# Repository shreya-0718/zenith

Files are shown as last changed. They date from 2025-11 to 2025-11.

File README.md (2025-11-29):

# zenith
### An STM32-based flight controller!
front

I made this project to explore more advanced hardware and firmware :)
Also, to get experience with the STM32 and its IDEs.

## Features:
- USB-C 
- MicroSD Card
- Servos: Two PWM Channels
- Sensors: I²C barometer (BMP580) and charger (BQ25883), SPI IMU (ICM-45686)
- Two programmable LEDs

## To Use:
- Install STM32CubeIDE here: https://www.st.com/en/development-tools/stm32cubeide.html
- Use the code in here as a starter, and build from there!
- Use the schematic below as a guide.

## Images:
full schem
stm32 schem
<br>
pcb!

<br>

front
back

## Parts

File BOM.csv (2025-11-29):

Item | Description | Link | Cost | Quantity
BMP580 | Barometric pressure sensor | https://www.lcsc.com/product-detail/C22391138.html | 1.08 | 1
Resistor | 330 | https://www.lcsc.com/product-detail/C105881.html | 0.12 | 1
LED | WS2812B-2020 SMD | https://www.lcsc.com/product-detail/C965555.html | 0.08 | 2
Capacitor | 1uF | https://jlcpcb.com/partdetail/53938-CL05A105KA5NQNC/C52923 | 0.01 | 4
Resistor | 5.1 K | https://jlcpcb.com/partdetail/26648-0402WGF5101TCE/C25905 | 0.01 | 2
Resistor | 10 | https://jlcpcb.com/partdetail/26487-0402WGF1002TCE/C25744 | 0.01 | 14
Capacitor | 100nF | https://jlcpcb.com/partdetail/1877-CL05B104KO5NNNC/C1525 | 0.01 | 11
Capacitor | 44nF | https://www.lcsc.com/product-detail/C49326689.html | 0.54 | 1
Capacitor | 10uF | https://jlcpcb.com/partdetail/2043-CL10A106MQ8NNNC/C1691 | 0.01 | 8
ICM-45686 | Motion sensor | https://www.lcsc.com/product-detail/C22459454.html | 8.55 | 1
TS-1088-AR02016 | Button | https://www.lcsc.com/product-detail/C720477.html | 0.08 | 2
Capacitor | 0.1uF | https://www.lcsc.com/product-detail/C76934.html | 0.12 | 1
Resistor | 100k | https://www.lcsc.com/product-detail/C60491.html | 0.06 | 1
Inductor | 1uH | https://www.lcsc.com/product-detail/C435392.html | 0.5 | 1
Capacitor | 22uF | https://www.lcsc.com/product-detail/C602037.html | 0.024 | 5
Screw Terminal | 01x02 | https://www.lcsc.com/product-detail/C557685 | 1.15 | 1
Connector | 01x03 | https://jlcpcb.com/partdetail/-PinSocket_1x03_P254mm_Vertical/C9900002703 | 0.01 | 2
Capacitor | 2.2uF | https://jlcpcb.com/partdetail/13164-CL05A225MQ5NSNC/C12530 | 0.0024 | 2
Resistor | 22.1k | https://jlcpcb.com/partdetail/YAGEO-RC0201FR0722K1L/C142019 | $0.00 | 1
Crystal Oscillator | 25MHz | https://jlcpcb.com/partdetail/YXC_CrystalOscillators-X322525MOB4SI/C9006 | 0.07 | 1
BQ25883RGER | Charging IC | https://jlcpcb.com/partdetail/TexasInstruments-BQ25883RGER/C544362 | 4.47 | 1
LED | Indicator | https://jlcpcb.com/partdetail/EverlightElec-16_213SDRC_S530_A3TR8/C71911 | 0.03 | 1
TF-01A | Micro SD Card | https://jlcpcb.com/partdetail/Korean_HropartsElec-TF01A/C91145 | 0.17 | 1
Resistor | 5.23k | https://jlcpcb.com/partdetail/301853-RC01W5231FT/C320948 | 0.001 | 1
Capacitor | 47uF | https://www.lcsc.com/product-detail/C49326689.html | 0.54 | 1
Capacitor | 20pF | https://jlcpcb.com/partdetail/72988-0201CG200J500NT/C71879 | 0.0007 | 4
Resistor | 10k | https://jlcpcb.com/partdetail/LIZElec-CR0201FH1002G/C100126 | 0.0005 | 1
LMR51431 | Power Management | https://jlcpcb.com/partdetail/TexasInstruments-LMR51430XDDCR/C5185863 | 0.97 | 1
Resistor | 30.1k | https://jlcpcb.com/partdetail/YAGEO-RC0201FR0730K1L/C273278 | 0.0008 | 1
Q13FC1350000401 | Crystal Oscillator | https://jlcpcb.com/partdetail/SeikoEpson-Q13FC1350000400/C49109464 | 0.25 | 1
FCM1608KF-601T04 | Ferrite Bead | https://jlcpcb.com/partdetail/TAITECH-FCM1608KF601T03/C141723 | 0.0046 | 1
STM32F722RETx | MCU | https://jlcpcb.com/partdetail/STMicroelectronics-STM32F722RET6/C118207 | 6.05 | 1
Inductor | 1.5uH | https://www.lcsc.com/product-detail/C3033018.html | 1.22 | 1
Inductor | 5.6uH | https://www.lcsc.com/product-detail/C18236327.html | 0.25 | 1
USB Receptacle | USB-C | https://jlcpcb.com/partdetail/DEALON-USB_TYPE_C007/C2927027 | 0.05 | 1
Resistor | 383 | https://jlcpcb.com/partdetail/416501-0201WMF3830TEE/C423551 | 0.0005 | 1

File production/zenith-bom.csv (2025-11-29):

Id | Designator | Footprint | Quantity | Designation | Supplier and ref
1 | C26,C24,C1,C25 | C_0402_1005Metric | 4 | 1uF
2 | R2,R1 | R_0201_0603Metric | 2 | 5.1 K
3 | R20,R21,R12,R5,R13,R16,R19,R10,R4,R17,R8,R3,R18,R6 | R_0201_0603Metric | 14 | 10K
4 | C30,C20,C32,C8,C19,C37,C22,C28,C29,C21,C31 | C_0201_0603Metric | 11 | 100nF
5 | C3 | C_0805_2012Metric | 1 | 44uF
6 | C9,C2,C7,C10,C27,C4,C6,C11 | C_0402_1005Metric | 8 | 10uF
7 | U4 | LGA-14_L3.0-W2.5-P0.50-TL | 1 | ICM-45686
8 | BOOT,RESET | SW-SMD_L3.9-W3.0-P4.45 | 2 | TS-1088-AR02016
9 | C15 | C_0201_0603Metric | 1 | 0.1uF
10 | R14 | R_0402_1005Metric | 1 | 100k
11 | LED1,LED2 | LED-SMD_4P-L2.0-W2.0-TL_WS2812B-2020 | 2 | WS2812B-2020
12 | L1 | L2520 | 1 | 1uH
13 | C17,C13,C12,C18,C14 | C_0805_2012Metric | 5 | 22uF
14 | J1 | TerminalBlock_Xinya_XY308-2.54-2P_1x02_P2.54mm_Horizontal | 1 | Screw_Terminal_01x02
15 | SERVO HEADERS,J2 | PinHeader_1x03_P2.54mm_Vertical | 2 | Conn_01x03
16 | C16,C23 | C_0402_1005Metric | 2 | 2.2uF
17 | R15 | R_0201_0603Metric | 1 | 22.1k
18 | X1 | CRYSTAL-SMD_4P-L3.2-W2.5-BL | 1 | X322525MOB4SI
19 | U3 | VFQFPN-24_L4.0-W4.0-P0.50-BL-EP2.8 | 1 | BQ25883RGER
20 | R23 | R_0201_0603Metric | 1 | 330
21 | D1 | LED_0402_1005Metric | 1 | LED
22 | SD Card | TF-SMD_TF-01A | 1 | TF-01A
23 | R11 | R_0201_0603Metric | 1 | 5.23K
24 | U2 | LGA-10_L2.0-W2.0-P0.50-TL_BMP580 | 1 | BMP580
25 | C5 | C_0805_2012Metric | 1 | 47uF
26 | C36,C35,C33,C34 | C_0201_0603Metric | 4 | 20pF
27 | R22 | R_0201_0603Metric | 1 | 10k
28 | U6 | SOT-23-6 | 1 | LMR51430
29 | R9 | R_0201_0603Metric | 1 | 30.1K
30 | X2 | FC-135R_L3.2-W1.5 | 1 | Q13FC1350000400
31 | L4 | L0603 | 1 | FCM1608KF-601T03
32 | U5 | LQFP-64_10x10mm_P0.5mm | 1 | STM32F722RETx
33 | L2 | IND-SMD_L4.0-W4.0-A | 1 | 1.5uH
34 | L3 | IND-SMD_L3.0-W3.0 | 1 | 5.6uH
35 | USB1 | USB-C-SMD_TYPE-C-6PIN-2MD-073 | 1 | TYPE-C 16PIN 2MD(073)
36 | R7 | R_0201_0603Metric | 1 | 383

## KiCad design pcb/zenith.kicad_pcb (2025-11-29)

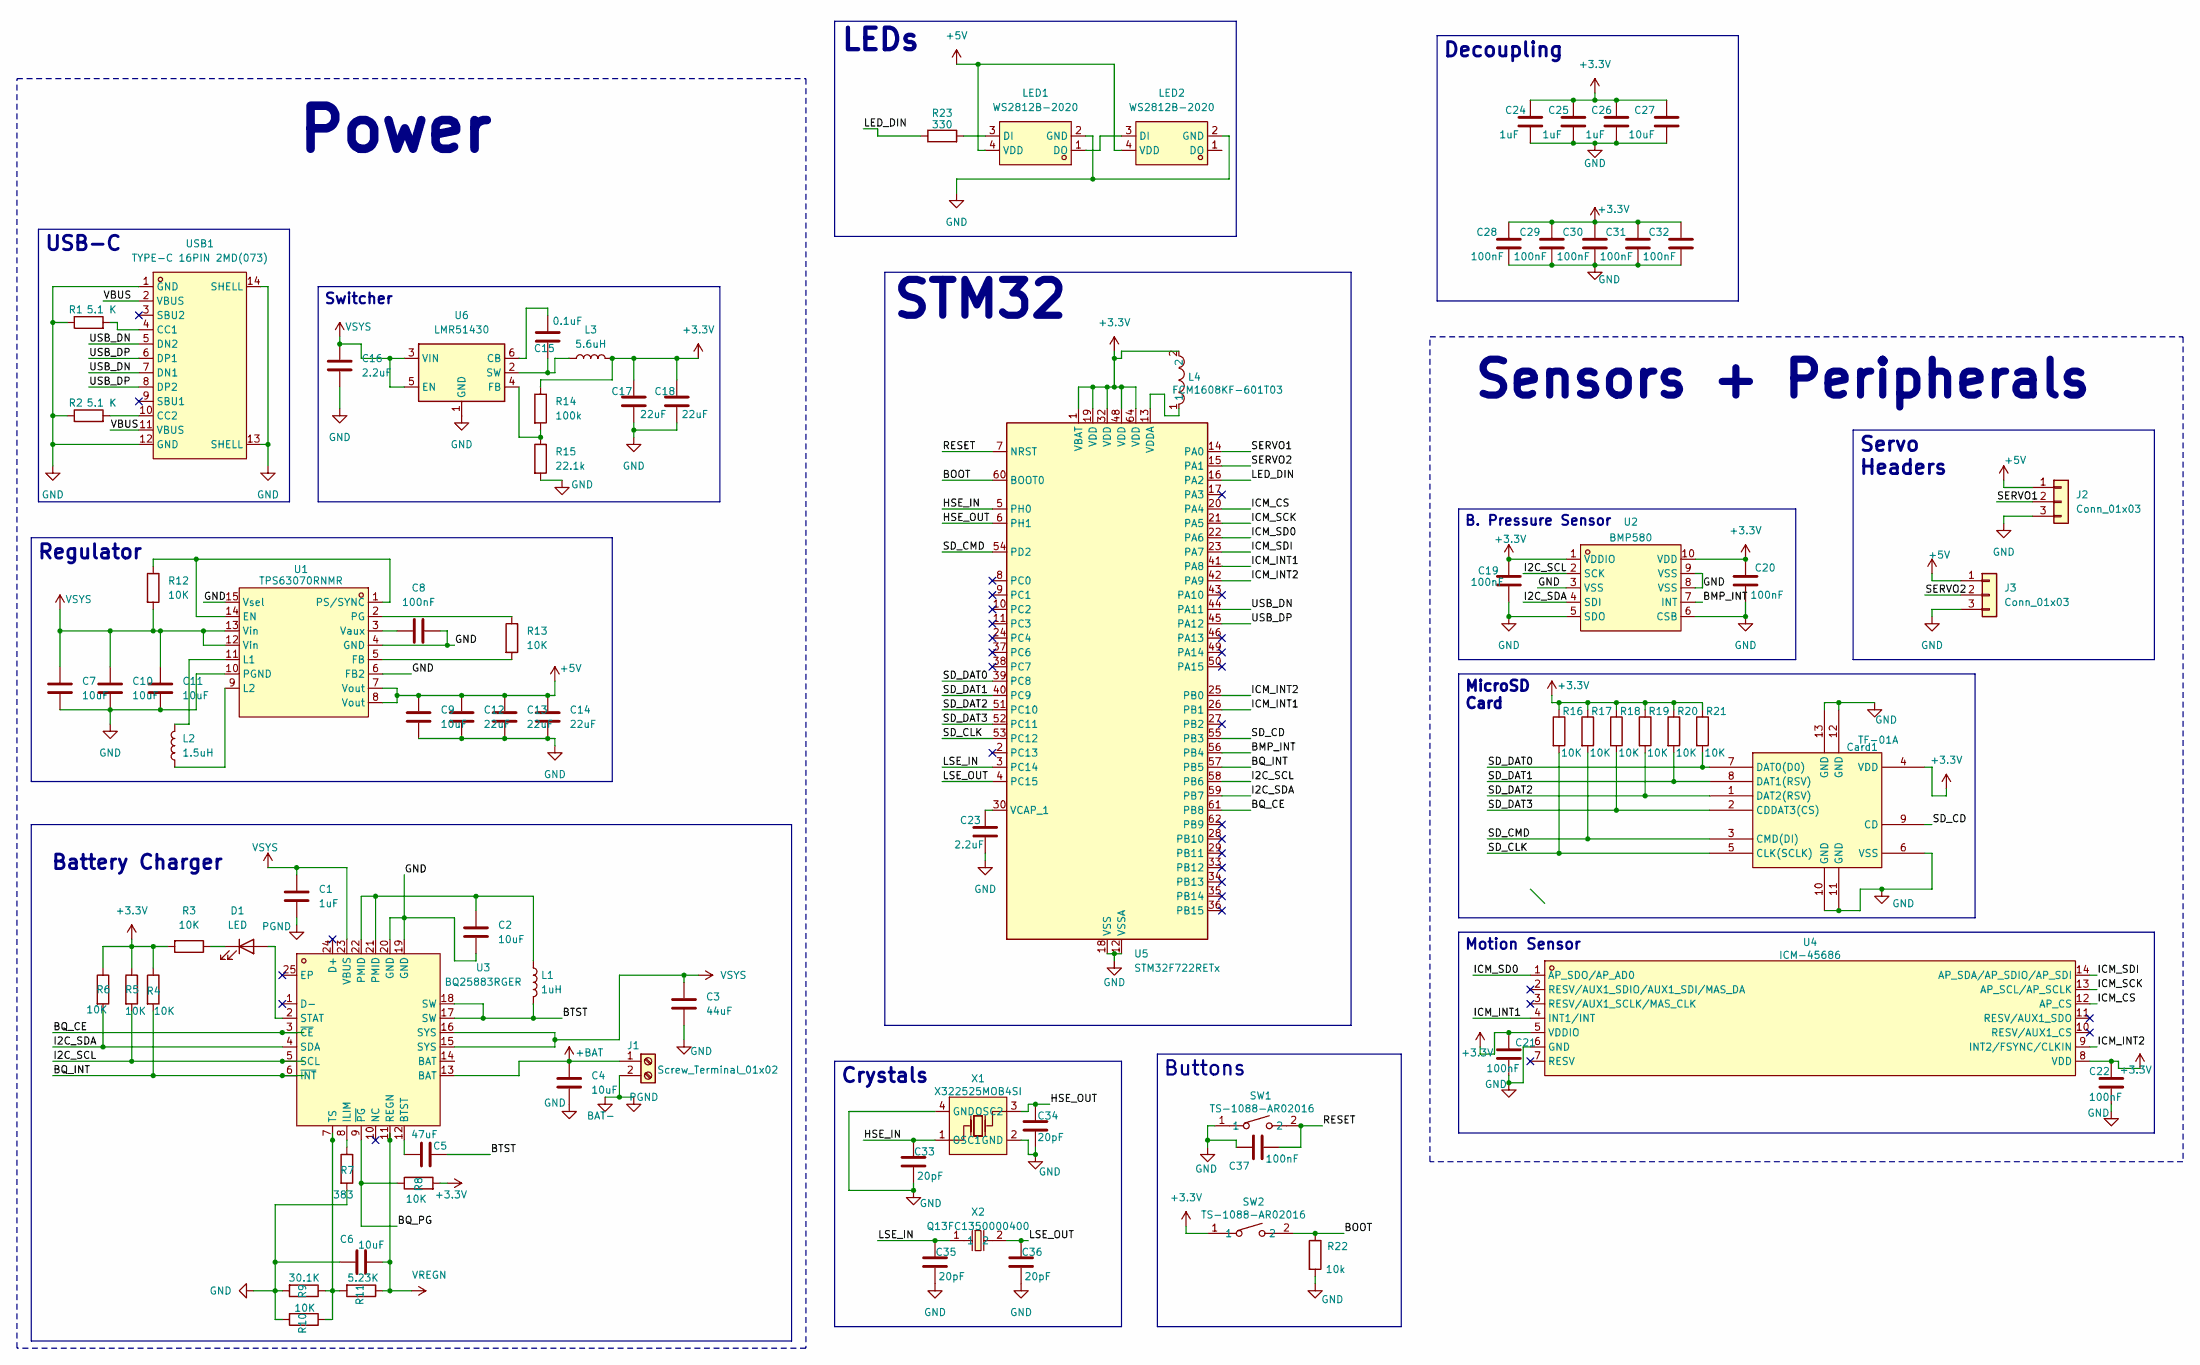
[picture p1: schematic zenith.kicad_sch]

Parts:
C1, C24, C25, C26: 1uF; C_0402_1005Metric
C2, C4, C6, C7, C9, C10, C11, C27: 10uF; C_0402_1005Metric
C3: 44uF; C_0805_2012Metric
C5: 47uF; C_0805_2012Metric
C8, C19, C20, C21, C22, C28, C29, C30, C31, C32, C37: 100nF; C_0201_0603Metric
C12, C13, C14, C17, C18: 22uF; C_0805_2012Metric
C15: 0.1uF; C_0201_0603Metric
C16, C23: 2.2uF; C_0402_1005Metric
C33, C34, C35, C36: 20pF; C_0201_0603Metric
Card1: TF-01A; TF-SMD_TF-01A; LCSC Part C91145
D1: LED; LED_0402_1005Metric
J1: Screw_Terminal_01x02; TerminalBlock_Xinya_XY308-2.54-2P_1x02_P2.54mm_Horizontal
J2, J3: Conn_01x03; PinHeader_1x03_P2.54mm_Vertical
L1: 1uH; L2520
L2: 1.5uH; IND-SMD_L4.0-W4.0-A
L3: 5.6uH; IND-SMD_L3.0-W3.0
L4: FCM1608KF-601T03; L0603; LCSC Part C141723
LED1, LED2: WS2812B-2020; LED-SMD_4P-L2.0-W2.0-TL_WS2812B-2020; LCSC Part C965555
R1, R2: 5.1 K; R_0201_0603Metric
R3, R4, R5, R6, R8, R10, R12, R13, R16, R17, R18, R19, R20, R21: 10K; R_0201_0603Metric
R7: 383; R_0201_0603Metric
R9: 30.1K; R_0201_0603Metric
R11: 5.23K; R_0201_0603Metric
R14: 100k; R_0402_1005Metric
R15: 22.1k; R_0201_0603Metric
R22: 10k; R_0201_0603Metric
R23: 330; R_0201_0603Metric
SW1, SW2: TS-1088-AR02016; SW-SMD_L3.9-W3.0-P4.45; LCSC Part C720477
U1: TPS63070RNMR; VQFN-HR-15_L3.0-W2.5-P0.50-BL_TPS63070RNMR; LCSC Part C109322
U2: BMP580; LGA-10_L2.0-W2.0-P0.50-TL_BMP580; LCSC Part C22391138
U3: BQ25883RGER; VFQFPN-24_L4.0-W4.0-P0.50-BL-EP2.8; LCSC Part C544362
U4: ICM-45686; LGA-14_L3.0-W2.5-P0.50-TL; LCSC Part C22459454
U5: STM32F722RETx; LQFP-64_10x10mm_P0.5mm
U6: LMR51430; SOT-23-6
USB1: TYPE-C 16PIN 2MD(073); USB-C-SMD_TYPE-C-6PIN-2MD-073; LCSC Part C2765186
X1: X322525MOB4SI; CRYSTAL-SMD_4P-L3.2-W2.5-BL; LCSC Part C9006
X2: Q13FC1350000400; FC-135R_L3.2-W1.5; LCSC Part C32346

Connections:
+3.3V: C17.1, C18.1, C19.1, C20.1, C21.1, C22.1, C24.1, C25.1, C26.1, C27.1, C28.1, C29.1, C30.1, C31.1, C32.1, Card1.4 (VDD), L3.2, L4.2, R3.2, R4.1, R5.1, R6.1, R8.2, R14.1, R16.1, R17.1, R18.1, R19.1, R20.1, R21.1, SW2.1, U2.1 (VDDIO), U2.10 (VDD), U4.5 (VDDIO), U4.8 (VDD), U5.1 (VBAT), U5.19 (VDD), U5.32 (VDD), U5.48 (VDD), U5.64 (VDD); also elsewhere on the board
+5V: C9.1, C12.1, C13.1, C14.1, J2.1, J3.1, LED1.4 (VDD), LED2.4 (VDD), U1.7 (Vout), U1.8 (Vout); also elsewhere on the board
+BAT: C4.1, J1.1, U3.13 (BAT)
/BMP_INT: U2.7 (INT), U5.56 (PB4)
/BOOT: R22.1, SW2.2, U5.60 (BOOT0); also elsewhere on the board
/BQ_CE: U3.3 (~CE), U5.61 (PB8)
/BQ_INT: R4.2, U3.6 (~INT), U5.57 (PB5)
/BQ_PG: R8.1, U3.9 (~PG)
/BTST: C5.2, L1.2, U3.17 (SW), U3.18 (SW)
/HSE_IN: C33.1, U5.5 (PH0), X1.1 (OSC1)
/HSE_OUT: C34.1, U5.6 (PH1), X1.3 (OSC2)
/I2C_SCL: R5.2, U2.2 (SCK), U3.5 (SCL), U5.58 (PB6)
/I2C_SDA: R6.2, U2.4 (SDI), U3.4 (SDA), U5.59 (PB7)
/ICM_CS: U4.12 (AP_CS), U5.20 (PA4)
/ICM_INT1: U4.4 (INT1/INT), U5.26 (PB1), U5.41 (PA8)
/ICM_INT2: U4.9 (INT2/FSYNC/CLKIN), U5.25 (PB0), U5.42 (PA9)
/ICM_SCK: U4.13 (AP_SCL/AP_SCLK), U5.21 (PA5)
/ICM_SD0: U4.1 (AP_SDO/AP_AD0), U5.22 (PA6)
/ICM_SDI: U4.14 (AP_SDA/AP_SDIO/AP_SDI), U5.23 (PA7)
/LED_DIN: R23.1, U5.16 (PA2)
/LSE_IN: C35.1, U5.3 (PC14), X2.1
/LSE_OUT: C36.1, U5.4 (PC15), X2.2
/RESET: C37.2, SW1.2, U5.7 (NRST); also elsewhere on the board
/SD_CD: Card1.9 (CD), U5.55 (PB3); also elsewhere on the board
/SD_CLK: Card1.5 (CLK(SCLK)), R16.2, U5.53 (PC12); also elsewhere on the board
/SD_CMD: Card1.3 (CMD(DI)), R17.2, U5.54 (PD2); also elsewhere on the board
/SD_DAT0: Card1.7 (DAT0(D0)), R21.2, U5.39 (PC8); also elsewhere on the board
/SD_DAT1: Card1.8 (DAT1(RSV)), R20.2, U5.40 (PC9); also elsewhere on the board
/SD_DAT2: Card1.1 (DAT2(RSV)), R19.2, U5.51 (PC10); also elsewhere on the board
/SD_DAT3: Card1.2 (CDDAT3(CS)), R18.2, U5.52 (PC11); also elsewhere on the board
/SERVO1: J2.2, U5.14 (PA0)
/SERVO2: J3.2, U5.15 (PA1); also elsewhere on the board
/USB_DN: U5.44 (PA11), USB1.5 (DN2), USB1.7 (DN1)
/USB_DP: U5.45 (PA12), USB1.6 (DP1), USB1.8 (DP2)
/VBUS: USB1.2 (VBUS), USB1.11 (VBUS)
BAT-: C1.1, J1.2
GND: C2.2, C3.2, C4.2, C6.1, C7.2, C8.2, C9.2, C10.2, C11.2, C12.2, C13.2, C14.2, C16.2, C17.2, C18.2, C19.2, C20.2, C21.2, C22.2, C23.2, C24.2, C25.2, C26.2, C27.2, C28.2, C29.2, C30.2, C31.2, C32.2, C33.2, C34.2, C35.2, C36.2, C37.1, Card1.6 (VSS), Card1.10 (GND), Card1.11 (GND), Card1.12 (GND), Card1.13 (GND), J2.3, J3.3, LED1.2 (GND), LED2.2 (GND), R1.1, R2.1, R7.2, R9.2, R10.2, R15.2, R22.2, SW1.1, U1.4 (GND), U1.6 (FB2), U1.10 (PGND), U1.15 (Vsel), U2.3 (VSS), U2.5 (SDO), U2.6 (CSB), U2.8 (VSS), U2.9 (VSS), U3.19 (GND), U3.20 (GND), U4.6 (GND), U5.12 (VSSA), U5.18 (VSS), U5.31 (VSS), U5.47 (VSS), U5.63 (VSS), U6.1 (GND), USB1.1 (GND), USB1.12 (GND), USB1.13 (SHELL), USB1.14 (SHELL), X1.2 (GND), X1.4 (GND); also elsewhere on the board
unnamed: C2.1, L1.1, U3.21 (PMID), U3.22 (PMID)
unnamed: D1.2 (A), U3.2 (STAT)
unnamed: D1.1 (K), R3.1
unnamed: LED1.3 (DI), R23.2
unnamed: LED1.1 (DO), LED2.3 (DI)
unnamed: R12.1, U1.1 (PS/SYNC), U1.14 (EN)
unnamed: R13.2, U1.5 (FB)
unnamed: L2.2, U1.11 (L1)
unnamed: L2.1, U1.9 (L2)
unnamed: R13.1, U1.2 (PG)
unnamed: C8.1, U1.3 (Vaux)
unnamed: C5.1, U3.12 (BTST)
unnamed: R7.1, U3.8 (ILIM)
unnamed: R9.1, R10.1, R11.2, U3.7 (TS)
unnamed: C23.1, U5.30 (VCAP_1)
unnamed: L4.1, U5.13 (VDDA)
unnamed: C15.1, U6.6 (CB)
unnamed: R14.2, R15.1, U6.4 (FB)
unnamed: C15.2, L3.1, U6.2 (SW)
unnamed: R1.2, USB1.4 (CC1)
unnamed: R2.2, USB1.10 (CC2)
VREGN: C6.2, R11.1, U3.11 (REGN)
VSYS: C1.2, C3.1, C7.1, C10.1, C11.1, C16.1, R12.2, U1.12 (Vin), U1.13 (Vin), U3.15 (SYS), U3.16 (SYS), U3.23 (VBUS), U6.3 (VIN), U6.5 (EN)

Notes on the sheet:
Power
Battery Charger
Sensors + Peripherals
LEDs
Crystals
USB-C
MicroSD Card
Decoupling
B. Pressure Sensor
Buttons
Servo Headers
Motion Sensor
Switcher
STM32
Regulator

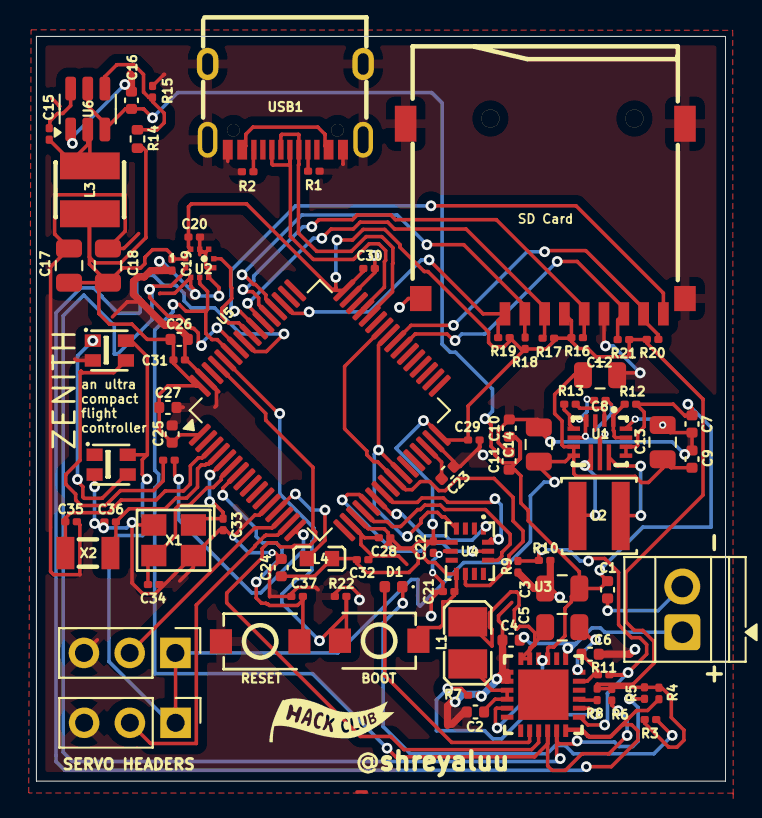
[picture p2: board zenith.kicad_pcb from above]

Board: 2 copper layers, 38.3 x 41.4 mm, 82 parts (0 on the bottom side), 60 nets.

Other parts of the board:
BOOT: TS-1088-AR02016; SW-SMD_L3.9-W3.0-P4.45
RESET: TS-1088-AR02016; SW-SMD_L3.9-W3.0-P4.45
SD Card: TF-01A; TF-SMD_TF-01A
SERVO HEADERS: Conn_01x03; PinHeader_1x03_P2.54mm_Vertical

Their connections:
+3.3V: BOOT.1, SD Card.4 (VDD); also elsewhere on the board
+5V: SERVO HEADERS.1; also elsewhere on the board
/BOOT: BOOT.2; also elsewhere on the board
/RESET: RESET.2; also elsewhere on the board
/SD_CD: SD Card.9 (CD); also elsewhere on the board
/SD_CLK: SD Card.5 (CLK(SCLK)); also elsewhere on the board
/SD_CMD: SD Card.3 (CMD(DI)); also elsewhere on the board
/SD_DAT0: SD Card.7 (DAT0(D0)); also elsewhere on the board
/SD_DAT1: SD Card.8 (DAT1(RSV)); also elsewhere on the board
/SD_DAT2: SD Card.1 (DAT2(RSV)); also elsewhere on the board
/SD_DAT3: SD Card.2 (CDDAT3(CS)); also elsewhere on the board
/SERVO2: SERVO HEADERS.2; also elsewhere on the board
GND: RESET.1, SD Card.6 (VSS), SD Card.10 (GND), SD Card.11 (GND), SD Card.12 (GND), SD Card.13 (GND), SERVO HEADERS.3; also elsewhere on the board

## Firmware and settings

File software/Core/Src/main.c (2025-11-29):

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
/* Includes ------------------------------------------------------------------*/
#include "main.h"


I2C_HandleTypeDef hi2c1;

SD_HandleTypeDef hsd1;

SPI_HandleTypeDef hspi1;

TIM_HandleTypeDef htim2;

HCD_HandleTypeDef hhcd_USB_OTG_FS;

void SystemClock_Config(void);
static void MPU_Config(void);
static void MX_GPIO_Init(void);
static void MX_I2C1_Init(void);
static void MX_SDMMC1_SD_Init(void);
static void MX_SPI1_Init(void);
static void MX_TIM2_Init(void);
static void MX_USB_OTG_FS_HCD_Init(void);
/**
  * @brief  The application entry point.
  * @retval int
  */
int main(void)
{

  /* MPU Configuration--------------------------------------------------------*/
  MPU_Config();

  /* MCU Configuration--------------------------------------------------------*/

  /* Reset of all peripherals, Initializes the Flash interface and the Systick. */
  HAL_Init();

  /* Configure the system clock */
  SystemClock_Config();

  /* Initialize all configured peripherals */
  MX_GPIO_Init();
  MX_I2C1_Init();
  MX_SDMMC1_SD_Init();
  MX_SPI1_Init();
  MX_TIM2_Init();
  MX_USB_OTG_FS_HCD_Init();
  /* USER CODE BEGIN 2 */

  HAL_TIM_PWM_Start(&htim2, TIM_CHANNEL_1);
  HAL_TIM_PWM_Start(&htim2, TIM_CHANNEL_2);
  HAL_I2C_Mem_Read(&hi2c1, 0x77 << 1, 0xD0, 1, &bmp_id, 1, HAL_MAX_DELAY);

  /* USER CODE END 2 */

  /* Infinite loop */
  /* USER CODE BEGIN WHILE */
  while (1)
  {
    // js flash on, off, 1s delay
//		HAL_GPIO_WritePin(GPIOA, GPIO_PIN_2, GPIO_PIN_SET); // LEDS ON
//		HAL_Delay(1000); // in ms
//		__HAL_TIM_SET_COMPARE(&htim2, TIM_CHANNEL_1, 1500);
//		__HAL_TIM_SET_COMPARE(&htim2, TIM_CHANNEL_2, 1500);
//		HAL_Delay(1000);
//		HAL_Delay(1000);

    HAL_I2C_Mem_Read(&hi2c1, 0x77 << 1, 0x04, 1, data, 3, HAL_MAX_DELAY);

    raw_pressure = ((uint32_t)data[0] << 16) |
                   ((uint32_t)data[1] << 8)  |
                   (uint32_t)data[2];

    if (raw_pressure > 50000) {
        HAL_GPIO_WritePin(GPIOA, GPIO_PIN_5, GPIO_PIN_SET);
    } else {
        HAL_GPIO_WritePin(GPIOA, GPIO_PIN_5, GPIO_PIN_RESET);
    }
    __HAL_TIM_SET_COMPARE(&htim2, TIM_CHANNEL_1, 1500);
    __HAL_TIM_SET_COMPARE(&htim2, TIM_CHANNEL_2, 1500);

    HAL_Delay(5000);

    /* USER CODE END WHILE */

    /* USER CODE BEGIN 3 */
  }
  /* USER CODE END 3 */
}

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
 /* MPU Configuration */

void MPU_Config(void)
{
  MPU_Region_InitTypeDef MPU_InitStruct = {0};

  /* Disables the MPU */
  HAL_MPU_Disable();

  /** Initializes and configures the Region and the memory to be protected
  */
  MPU_InitStruct.Enable = MPU_REGION_ENABLE;
  MPU_InitStruct.Number = MPU_REGION_NUMBER0;
  MPU_InitStruct.BaseAddress = 0x0;
  MPU_InitStruct.Size = MPU_REGION_SIZE_4GB;
  MPU_InitStruct.SubRegionDisable = 0x87;
  MPU_InitStruct.TypeExtField = MPU_TEX_LEVEL0;
  MPU_InitStruct.AccessPermission = MPU_REGION_NO_ACCESS;
  MPU_InitStruct.DisableExec = MPU_INSTRUCTION_ACCESS_DISABLE;
  MPU_InitStruct.IsShareable = MPU_ACCESS_SHAREABLE;
  MPU_InitStruct.IsCacheable = MPU_ACCESS_NOT_CACHEABLE;
  MPU_InitStruct.IsBufferable = MPU_ACCESS_NOT_BUFFERABLE;

  HAL_MPU_ConfigRegion(&MPU_InitStruct);
  /* Enables the MPU */
  HAL_MPU_Enable(MPU_PRIVILEGED_DEFAULT);

}

/**
  * @brief  This function is executed in case of error occurrence.
  * @retval None
  */
void Error_Handler(void)
{
  /* USER CODE BEGIN Error_Handler_Debug */
  /* User can add his own implementation to report the HAL error return state */
  __disable_irq();
  while (1)
  {
  }
  /* USER CODE END Error_Handler_Debug */
}
#ifdef USE_FULL_ASSERT
/**
  * @brief  Reports the name of the source file and the source line number
  *         where the assert_param error has occurred.
  * @param  file: pointer to the source file name
  * @param  line: assert_param error line source number
  * @retval None
  */
void assert_failed(uint8_t *file, uint32_t line)
{
  /* USER CODE BEGIN 6 */
  /* User can add his own implementation to report the file name and line number,
     ex: printf("Wrong parameters value: file %s on line %d\r\n", file, line) */
  /* USER CODE END 6 */
}
#endif /* USE_FULL_ASSERT */

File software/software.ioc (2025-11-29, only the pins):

Mcu.UserName=STM32F722RETx
PA0-WKUP.Signal=S_TIM2_CH1_ETR
PA1.Signal=S_TIM2_CH2
PA11.Signal=USB_OTG_FS_DM
PA12.Signal=USB_OTG_FS_DP
PA2.Signal=GPIO_Output
PA4.Signal=SPI1_NSS
PA5.Signal=SPI1_SCK
PA6.Signal=SPI1_MISO
PA7.Signal=SPI1_MOSI
PB0.GPIO_Label=ICM_INT2
PB0.Signal=GPXTI0
PB1.GPIO_Label=ICM_INT1
PB1.Signal=GPXTI1
PB3.GPIO_Label=SD_CS
PB3.Signal=GPIO_Input
PB4.GPIO_Label=BMP_INT
PB4.Signal=GPXTI4
PB5.GPIO_Label=BQ_INT
PB5.Signal=GPXTI5
PB6.Signal=I2C1_SCL
PB7.Signal=I2C1_SDA
PB8.GPIO_Label=BQ_CE
PB8.Signal=GPIO_Output
PC10.Signal=SDMMC1_D2
PC11.Signal=SDMMC1_D3
PC12.Signal=SDMMC1_CK
PC14-OSC32_IN.Signal=RCC_OSC32_IN
PC15-OSC32_OUT.Signal=RCC_OSC32_OUT
PC8.Signal=SDMMC1_D0
PC9.Signal=SDMMC1_D1
PD2.Signal=SDMMC1_CMD
PH0-OSC_IN.Signal=RCC_OSC_IN
PH1-OSC_OUT.Signal=RCC_OSC_OUT

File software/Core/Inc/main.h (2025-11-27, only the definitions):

#define ICM_INT2_Pin GPIO_PIN_0
#define ICM_INT2_GPIO_Port GPIOB
#define ICM_INT1_Pin GPIO_PIN_1
#define ICM_INT1_GPIO_Port GPIOB
#define SD_CS_Pin GPIO_PIN_3
#define SD_CS_GPIO_Port GPIOB
#define BMP_INT_Pin GPIO_PIN_4
#define BMP_INT_GPIO_Port GPIOB
#define BQ_INT_Pin GPIO_PIN_5
#define BQ_INT_GPIO_Port GPIOB
#define BQ_CE_Pin GPIO_PIN_8
#define BQ_CE_GPIO_Port GPIOB

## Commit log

2025-11-22 wired more of the schematic, added some more parts
    [zenith.kicad_sch]
2025-11-22 organization, more wires!
    [zenith.kicad_sch]
2025-11-23 finished schematic
    [zenith.kicad_sch]
2025-11-23 placed components, began routing
    [zenith.kicad_pcb, zenith.kicad_sch]
2025-11-23 finished pcb
    [zenith.kicad_pcb]
2025-11-24 added LEDs, finished pcb
    [zenith.kicad_pcb, zenith.kicad_sch]
2025-11-24 minor fixes
    [zenith.kicad_pcb]
2025-11-24 more editing silkscreen
    [zenith.kicad_pcb, zenith.kicad_sch]
2025-11-24 organizing repo
    [zenith.kicad_pcb, zenith.kicad_sch]
2025-11-24 fixed gitignore issues
    [BOM.csv]
2025-11-24 remove extra pcb file
    [zenith.kicad_pcb]
2025-11-27 installed basics for stm32 code
2025-11-28 learning basic stm32 code
2025-11-29 added production files
    [zenith-B_Cu.gbr, zenith-B_Mask.gbr, zenith-B_Paste.gbr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]
2025-11-29 updated bom
    [BOM.csv, zenith-bom.csv]

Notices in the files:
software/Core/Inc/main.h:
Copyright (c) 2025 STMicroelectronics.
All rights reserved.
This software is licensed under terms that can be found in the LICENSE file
